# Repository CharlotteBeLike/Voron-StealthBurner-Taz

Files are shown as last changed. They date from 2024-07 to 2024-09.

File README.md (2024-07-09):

This was a fun challenge to put a Stealthburner onto my Taz 6.<br><br>
This mod may possibly be adaptable to the Taz Workhorse, Taz Pro, Taz Pro S, Taz Pro XT, Taz 5, Taz 4, Taz 3, Mini v1.04, Mini v1.03, and Kittaz :)<br>
Please be aware that none of this is perfect and you might have a few bumps along the way while building this. THERE ARE NO DOCS, so you will have to use the CAD model to assemble<br><br>

Printables: https://www.printables.com/model/543772-taz-56-to-stealthburner-v2<br><br>


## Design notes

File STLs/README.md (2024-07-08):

# Filename Nomenclature

| Category | Item | Amount |
|---|---|--|
| \*.stl | Base color |
| [a]\_\*.stl | Accent color |
| [c]\_\*.stl | Clear/Translucent (light can penetrate) |

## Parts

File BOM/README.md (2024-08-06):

# BOM

| Category | Item | Amount |
|---|---|---|
| Hardware | M3 X D5.0 X L4.0 Heat Set Insert| 22 |
| Hardware	| M3 Spring-Loaded T-Nut | 8 |
| Hardware	| M5 Spring-Loaded T-Nut	| 4 |
| Hardware	| Hotend Mounting Screws (M2.5/M3)	| 2-4 |
| Hardware	| M2x8 SHCS	| 2 |
| Hardware	| M2x10 SHCS	| 2 |
| Hardware	| M3x6 FHCS	| 3 |
| Hardware	| M3x6 BHCS	| 1 |
| Hardware	| M3x8 SHCS	| 14 |
| Hardware	| M3x10 SHCS	| 2 |
| Hardware	| M3x12 SHCS	| 12 |
| Hardware	| M3x16 SHCS	| 2 |
| Hardware	| M3x20 SHCS	| 1 |
| Hardware	| M3x25 SHCS	| 6 |
| Hardware	| M3x30 SHCS	| 1 |
| Hardware	| M3x40 SHCS	| 1 |
| Hardware	| M3x50 SHCS	| 2 |
| Hardware	| M3 Washer	| 1 |
| Hardware	| M3 Nut	| 2 |
| Hardware	| M5x12 SHCS	| 6 |
| Hardware	| 350mm 2020 V-Slot Extrusion	| 1 |
| Electronics	| NEMA14 36mm Round Pancake Motor with 10 tooth gear 20mm	| 1 |
| Electronics	| NEMA17 Stepper Motor	| 2 |
| Electronics	| DC 24V 5015 Centrefugal Fan	| 1 |
| Electronics	| DC 24V 4010 Axial Fan	| 1 |
| Electronics	| NeoPixel RGBW Mini Button PCB	| 3 |
| Electronics	| ADXL345 Accelerometer	| 1 |
| Electronics	| Rapido HF	| 1 |
| Electronics	| BL Touch	| 1 |
| Misc.	| Black Filament	| 1 |
| Misc.	| Lime Filament	| 1 |
| Misc.	| Lime Filament	| 1 |
| Misc.	| 6x3mm Magnet	| 1 |
| Misc.	| 3mmx4mm PTFE Tube 5M Length	| 1 |
| Printed | Parts	Z Carriage Right	| 1 |
| Printed | Parts	Z Carriage Left	| 1 |
| Printed | Parts	Rail Endstop	| 1 |
| Printed | Parts	Rail Endstop Mount	| 1 |
| Printed | Parts	Toolhead Hotend Front	| 1 |
| Printed | Parts	Toolhead Hotend Back	| 1 |
| Printed | Parts	Tensioner Slider	| 1 |
| Printed | Parts	X Carriage Frame Right	| 1 |
| Printed | Parts	X Carriage Frame Left	| 1 |
| Printed | Parts	Main Body	| 1 |
| Printed | Parts	Motor Plate	| 1 |
| Printed | Parts	[a]_Guilder A	| 1 |
| Printed | Parts	[a]_Guilder B	| 1 |
| Printed | Parts	[a]_Latch	| 1 |
| Printed | Parts	[a]_Shuttle	| 1 |
| Printed | Parts	[a]_Cover	| 1 |
| Printed | Parts	[c]_LED Carrier	| 1 |
| Printed | Parts	[c]_LED Diffuser Mask	| 1 |
| Printed | Parts	[c]_LED Diffuser | 1 |
| Printed | Parts	Cable Cover	| 1 |
| Printed | Parts	PCB Spacer (Optional)	| 1 |
| Printed | Parts	CW2 Chain Anchor For CANBUS (Optional)	| 1 |
| Printed | Parts	Printed Part For CAN Cable (Optional)	| 1 |
| Printed | Parts	Inductive Mount (Optional)	| 1 |
| Printed | Parts	BL Touch Mount (Optional)	| 1 |
| Printed | Parts	ADXL345 Screw Spacer (Optional)	| 2 |
| Motion	| 350mm MGN12H Linear Rail	| 1 |
| Motion	| Timing Pulley 20 teeth 5mm Bore	| 2 |
| Motion	| GATES-2GT	| 2 |
| Motion	| BMG Extruder Insides	| 1 |
| Cables	| MicroFit3 Male Pin	| 3 |
| Cables	| MicroFit3 Female Pin	| 3 |
| Cables	| MicroFit3 Connector Receptical 3 Position	| 1 |
| Cables	| MicroFit3 Connector Plug 3 Position	| 1 |
| Cables	| 30AWG PTFE Cable (3ft total)	| 1 |
| Cables	| 24AWG PTFE Cable (30ft total)	| 1 |

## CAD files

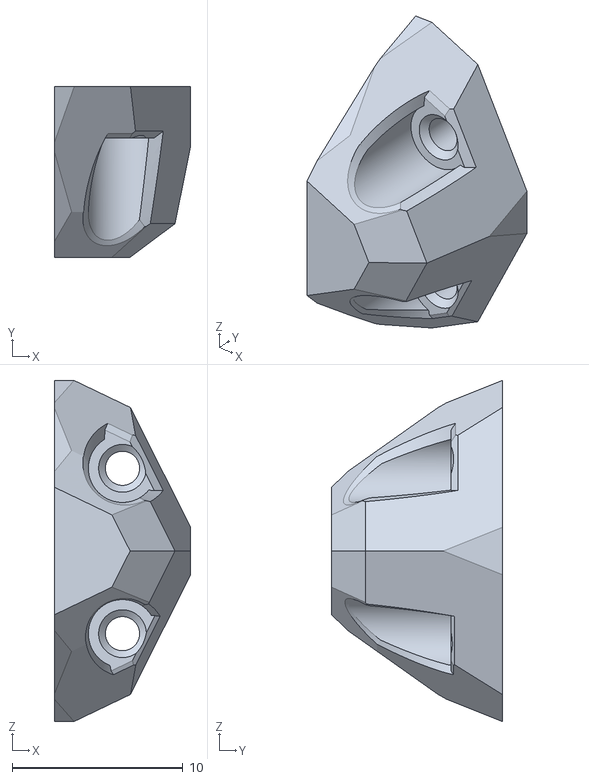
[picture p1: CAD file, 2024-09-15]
STLs/Rail Endstop.stl
8.00 x 10.0 x 20.0

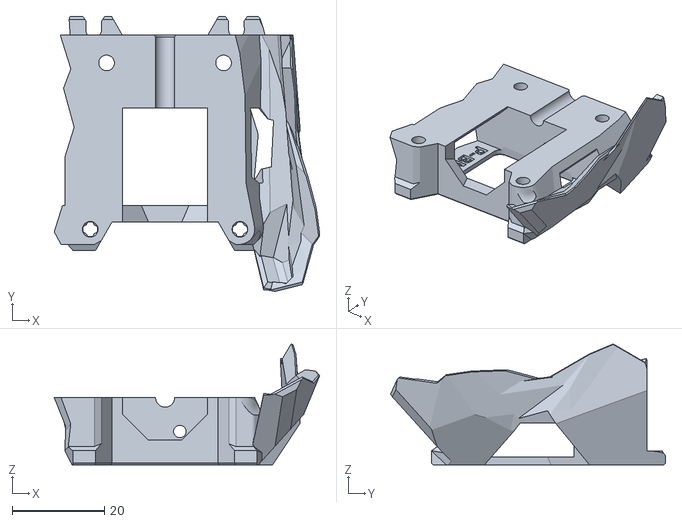
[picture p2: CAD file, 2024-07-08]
STLs/Stealthburner Printheads/phaetus_bmo/stealthburner_printhead_phaetus_bmo_rear_cw2.stl
57.7 x 59.7 x 26.3

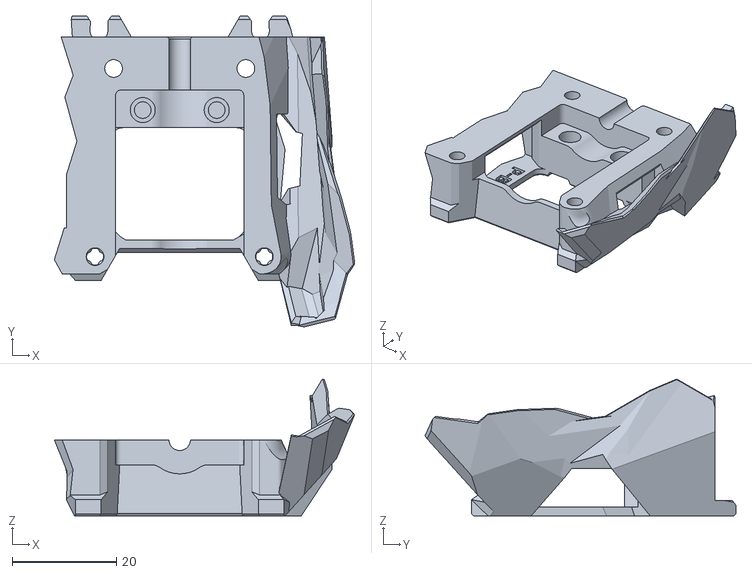
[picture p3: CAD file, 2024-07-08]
STLs/Stealthburner Printheads/phaetus_bms/stealthburner_printhead_phaetus_bms7_rear_cw2.stl
57.7 x 59.7 x 26.3

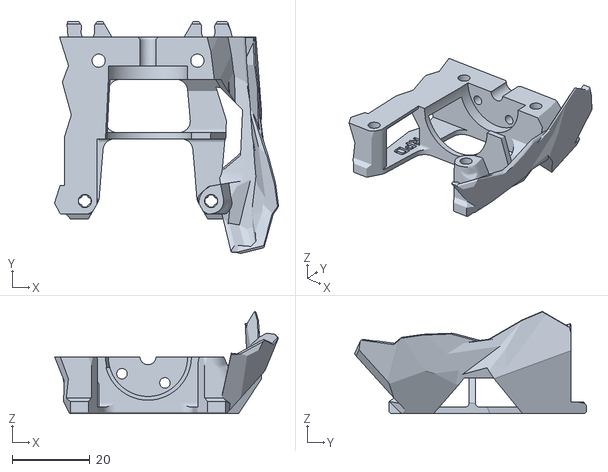
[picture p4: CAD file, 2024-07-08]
STLs/Stealthburner Printheads/phaetus_rapido/stealthburner_printhead_rapido_rear_cw2.stl
57.7 x 59.7 x 26.3

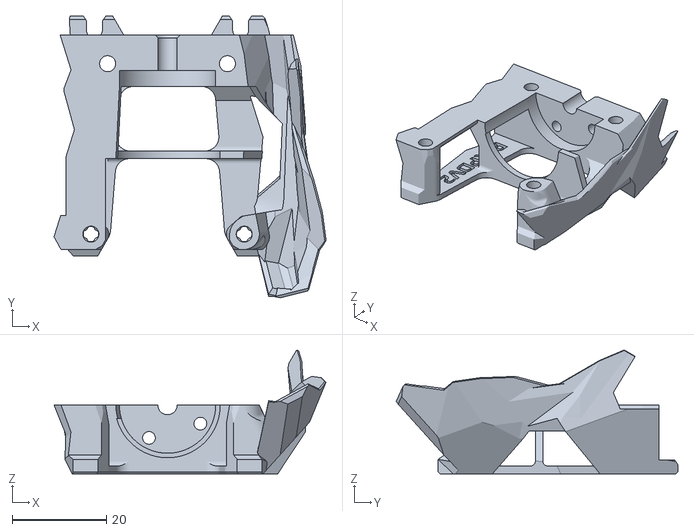
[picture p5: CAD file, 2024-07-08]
STLs/Stealthburner Printheads/phaetus_rapido_v2/stealthburner_printhead_rapido_v2_rear_cw1.stl
57.7 x 59.7 x 26.3

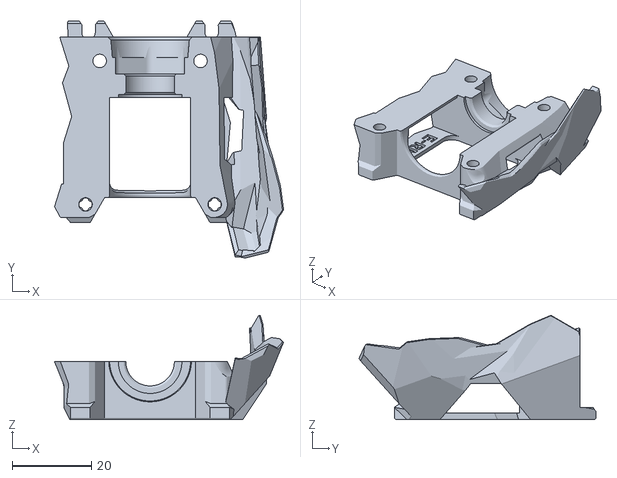
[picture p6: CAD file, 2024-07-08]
STLs/Stealthburner Printheads/revo_micro/stealthburner_printhead_revo_micro_rear_cw2.stl
57.7 x 59.7 x 26.3

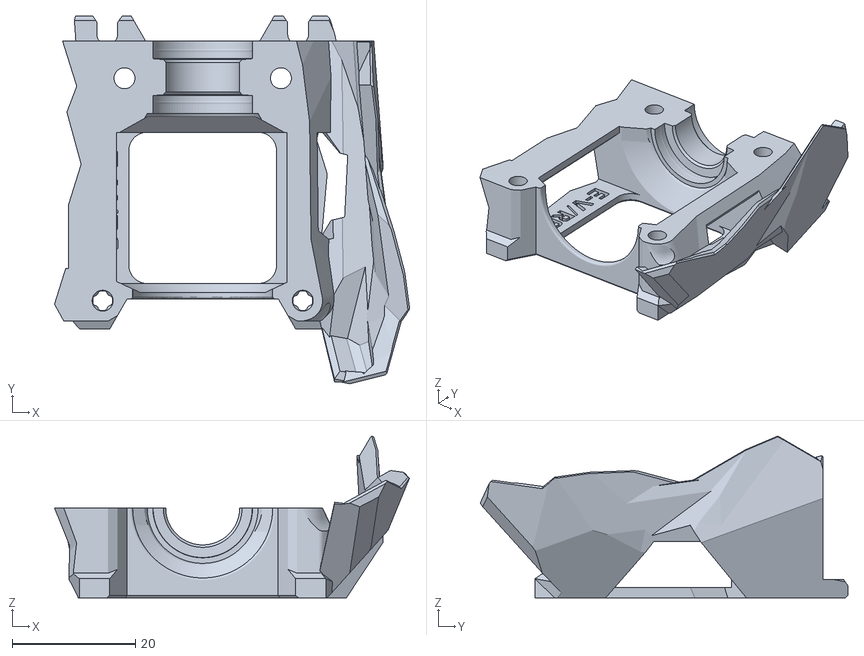
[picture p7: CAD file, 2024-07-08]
STLs/Stealthburner Printheads/revo_six_and_v6/stealthburner_printhead_v6_r6_rear_cw2.stl
57.7 x 59.7 x 26.3

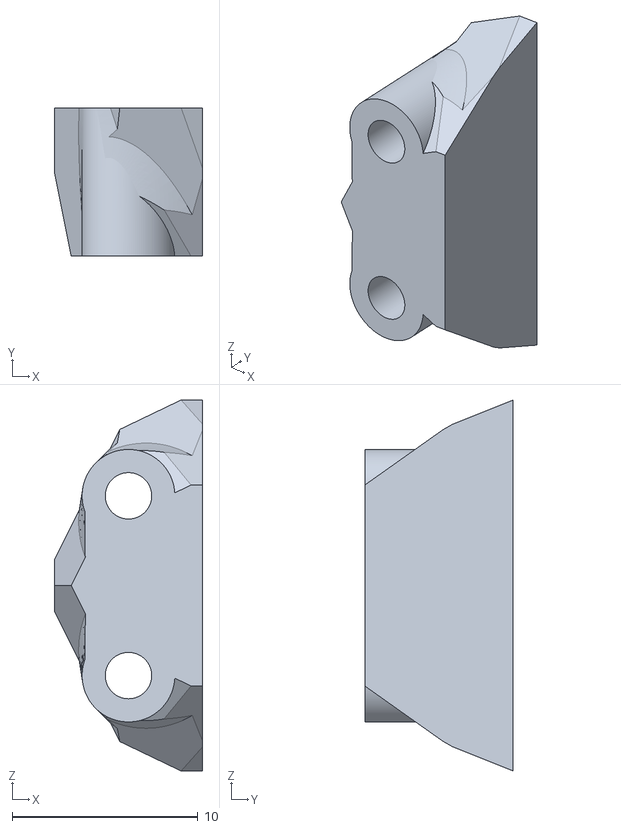
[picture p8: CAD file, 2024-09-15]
STLs/Rail Endstop Mount.stl
8.00 x 8.00 x 20.0

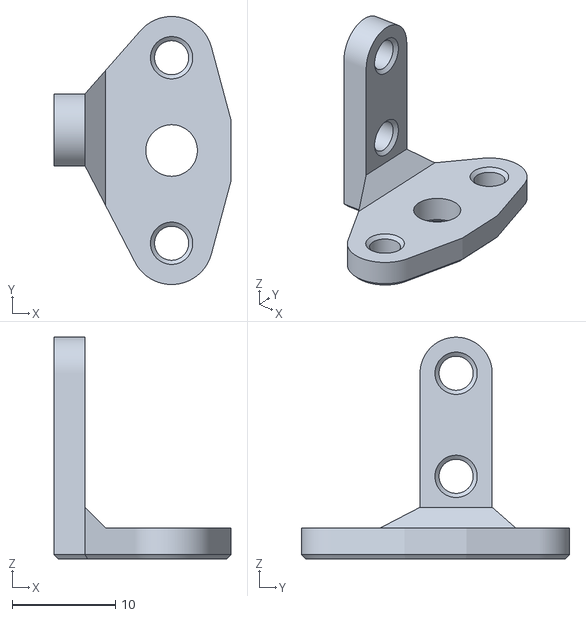
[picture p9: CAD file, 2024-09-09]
STLs/BL Touch Mount.stl
17.1 x 26.0 x 21.5

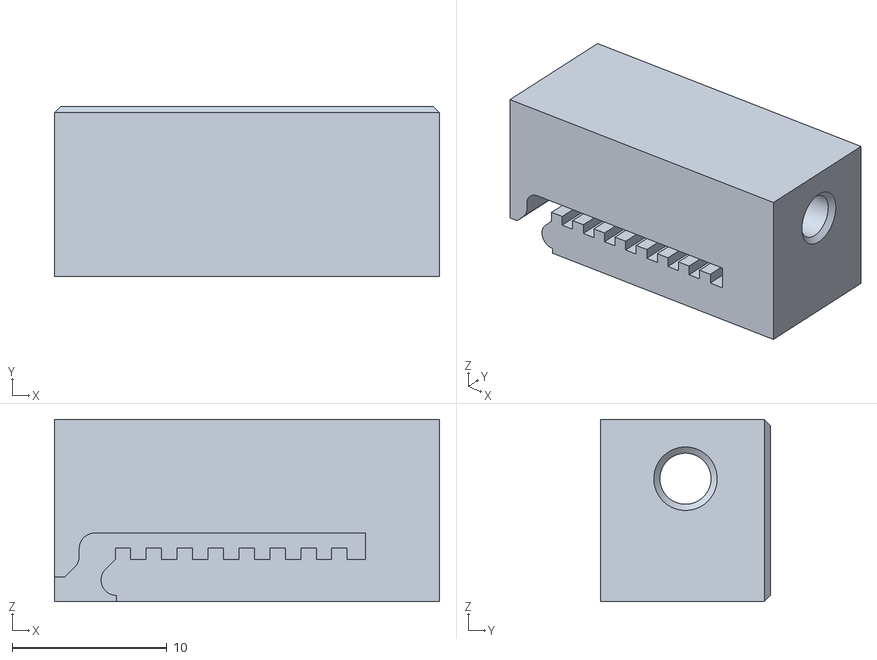
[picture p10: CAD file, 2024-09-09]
STLs/Tension Slider.stl
24.9 x 11.0 x 11.8

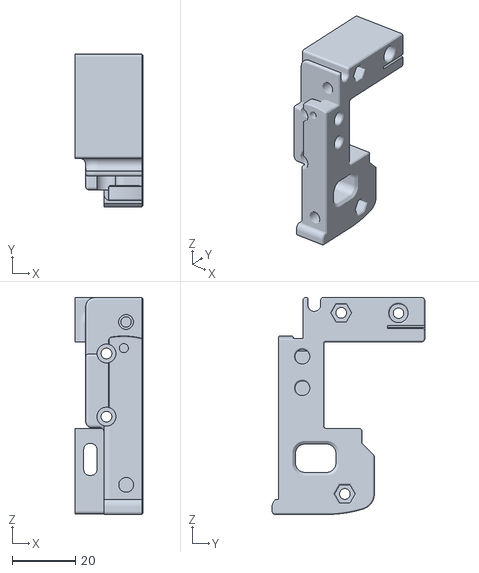
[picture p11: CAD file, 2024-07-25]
STLs/X Carriage Frame Right.stl
21.6 x 48.4 x 68.8

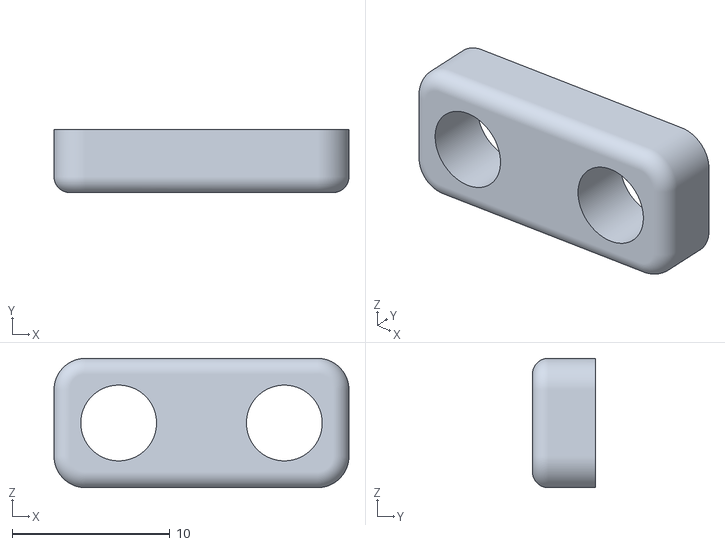
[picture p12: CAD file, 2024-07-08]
STLs/Inductive Mount.stl
18.7 x 4.00 x 8.20

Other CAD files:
STLs/Stealthburner Printheads/phaetus_dragon/stealthburner_printhead_dragon_rear_cw2.stl
STLs/Stealthburner Printheads/revo_voron/stealthburner_printhead_revo_voron_rear_cw2.stl
STLs/Stealthburner Printheads/phaetus_bmo/stealthburner_printhead_phaetus_bmo_rear_cw1.stl
STLs/Stealthburner Printheads/phaetus_bms/stealthburner_printhead_phaetus_bms6_rear_cw2.stl
STLs/Stealthburner Printheads/phaetus_rapido_v2/stealthburner_printhead_rapido_v2_rear_cw2.stl
STLs/X Carriage Frame Left.stl
STLs/ADXL345 Mount.stl
STLs/ADXL345 Screw Spacer.stl
STLs/CW2 Chain Anchor For CANBUS.stl
STLs/Cable Cover For PCB.stl
STLs/Printed Part For CAN Cable.stl
STLs/[c]_LED Carrier.stl
STLs/[c]_LED Diffuser Mask.stl
STLs/[c]_LED Diffuser.stl

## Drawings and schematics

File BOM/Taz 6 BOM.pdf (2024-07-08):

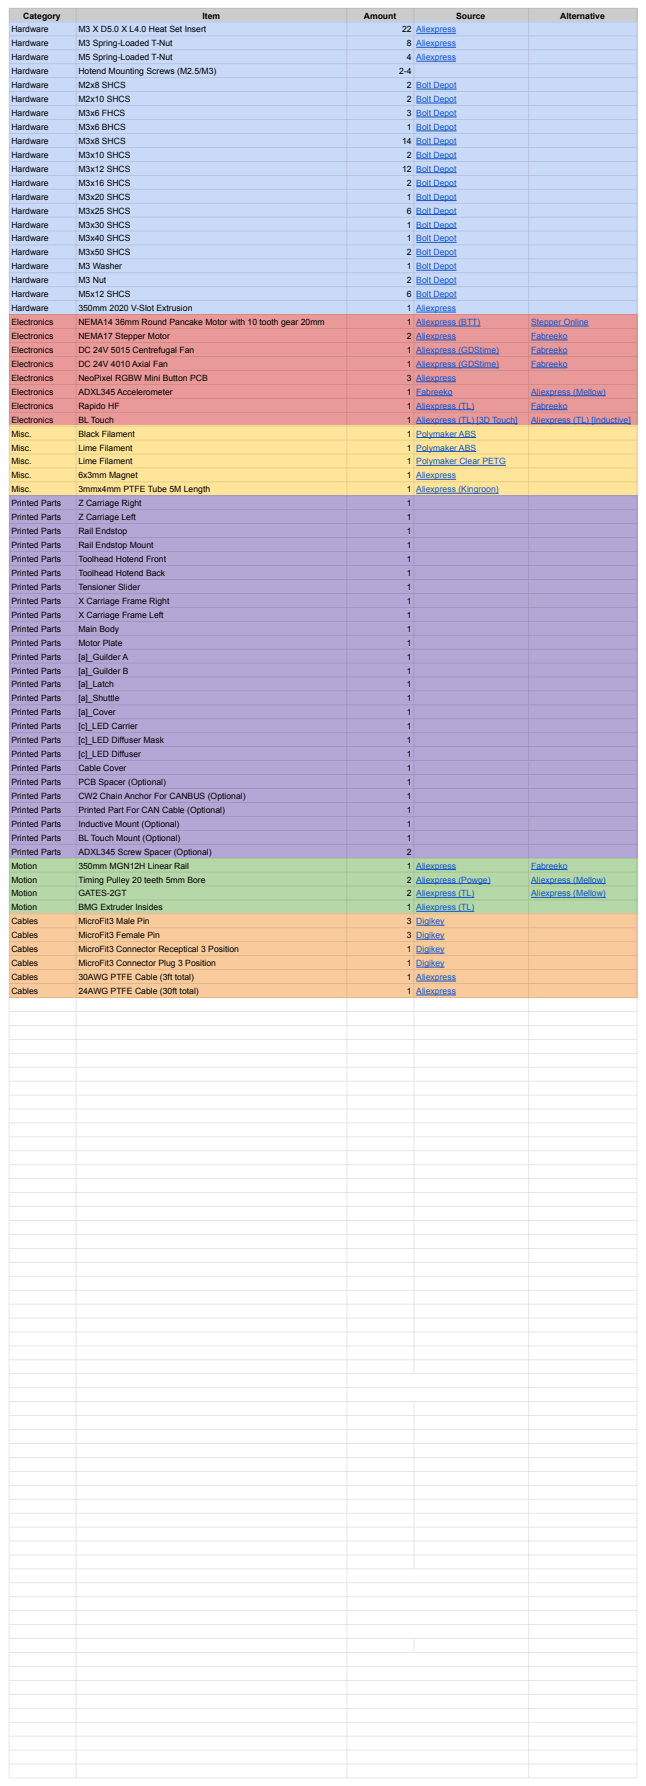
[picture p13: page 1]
Category; Item; Amount; Source; Alternative Hardware; M3 X D5.0 X L4.0 Heat Set Insert; 22 Aliexpress Hardware; M3 Spring-Loaded T-Nut; 8 Aliexpress Hardware; M5 Spring-Loaded T-Nut; 4 Aliexpress Hardware; Hotend Mounting Screws (M2.5/M3); 2-4 Hardware; M2x8 SHCS; 2 Bolt Depot Hardware; M2x10 SHCS; M3x6 FHCS; 3 Bolt Depot Hardware; M3x6 BHCS; 1 Bolt Depot Hardware; M3x8 SHCS; 14 Bolt Depot Hardware; M3x10 SHCS; M3x12 SHCS; 12 Bolt Depot Hardware; M3x16 SHCS; M3x20 SHCS; M3x25 SHCS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

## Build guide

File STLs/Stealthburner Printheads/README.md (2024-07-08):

# Printheads for Stealthburner.

Choose files containing ***front*** based on your hotend and ***rear_cw1*** / ***rear_cw2*** based on whether you're using the original Clockwork (CW1) or the new Clockwork2 (CW2) extruder.

## Printhead Compatibility:

| Hotend | Compatible Parts | Mounting Hardware | Notes |
| :---: | :---: | :---: | :---:
| Phaetus/Trianglelab Dragon ST/SF/HF | (P-DRG) | 4x M2.5x8mm | Remove the screws attaching the groove-mount adaptor to access the hard mounting points. |
| Phaetus BMO | (P-BMO) | 4x M2.5x8mm | Unscrew the groove-mount adaptor to access the hard mounting points. |
| Phaetus BMS (6 fins) | (P-BMS6) | 2x M3x12mm | Phaetus has two versions of the BMS; Count the number of fins on your hotend to determine your version. |
| Phaetus BMS (7 fins) | (P-BMS7) | 2x M3x12mm | Phaetus has two versions of the BMS; Count the number of fins on your hotend to determine your version. |
| Phaetus Rapido | (P-RPD) | 4x M2.5x8mm | Only the standard Rapido is supported (No UHF support). See the additional note about [heatsink orientations](phaetus_rapido/README.md). |
| E3D Revo Micro | (E-RM) | M12x1.5mm Plastic Nut | If your mount nut has a ridge on it, put that to the top. |
| E3D Revo Six | (E-V/R6) | N/A |  |
| E3D V6 | (E-V/R6) | N/A |  |
| E3D Revo Voron | (E-RV) | 4x M3x8mm |  |

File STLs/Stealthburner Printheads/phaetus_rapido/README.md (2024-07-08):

## Phaetus Rapido High Flow mount

### BOM

- One front printed part
- One rear printed part
- Heatset inserts
- Four M2.5x8 socket screws, which should be provided in your Rapido kit
- Two M3x12 socket screws
- PTFE tube

### Instructions

- Add two heatset inserts on the front printed part. Add an additional two if you plan to use the ADXL PCB mount.
- Remove the adapter and bowden collet from the Rapido's heatsink by unscrewing the two M2.5x5 screws:
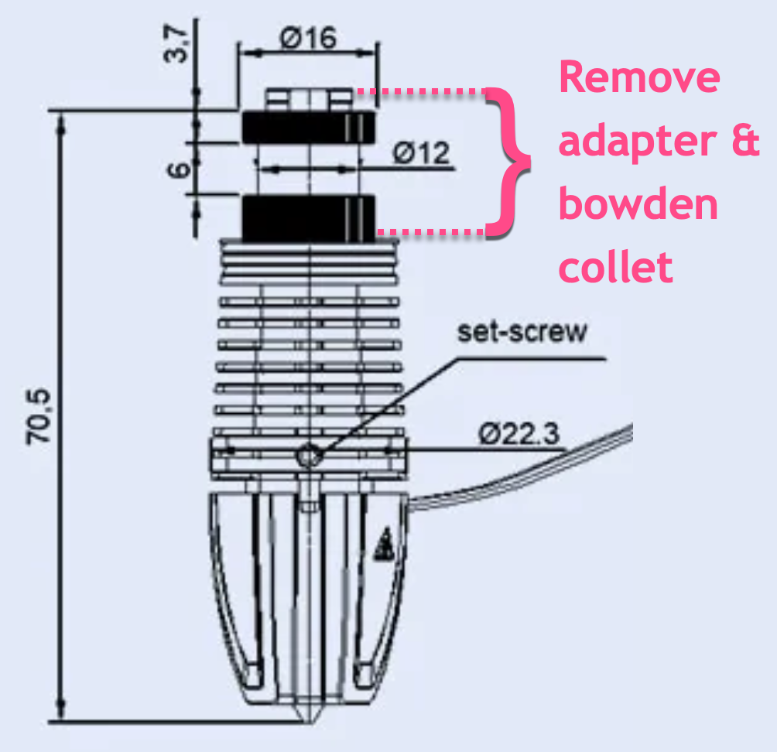
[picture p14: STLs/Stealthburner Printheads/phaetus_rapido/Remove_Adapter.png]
Remove adapter
  
- Place the hotend in the front printed part and secure it by screwing two M2.5x8 screws into the heatsink.
- Secure the front and rear printed parts together with two M3x12 screws.
- Secure the hotend with the rear part by screwing two M2.5x8 screws into the heatsink.
- Insert the PFTE tube at the top of the mount.

### A note about Rapido orientations

Depending on where the Rapido is sourced, it may come in one of two _unsupported_ heatsink orientations.

To change the orientation of heatsink to a supported orientation:

1. Loosen the grub screw on the side.
2. Remove the 3 screws around the heater core.
3. Rotate the heatsink +/- 120° into the correct orientation (see the pictures below).
4. Install and _gently tighten_ the 3 screws around the heater core.
5. _Gently tighten_ the side grub screw.
6. **Be careful not to over-tighten any screws when reassembling.**  Over-tightening can cause the heatbreak to bend and potentially restrict the filament path. Checking for smooth filament movement through a cold hotend without a nozzle is recommended prior to reinstalling the Rapido into the printhead.

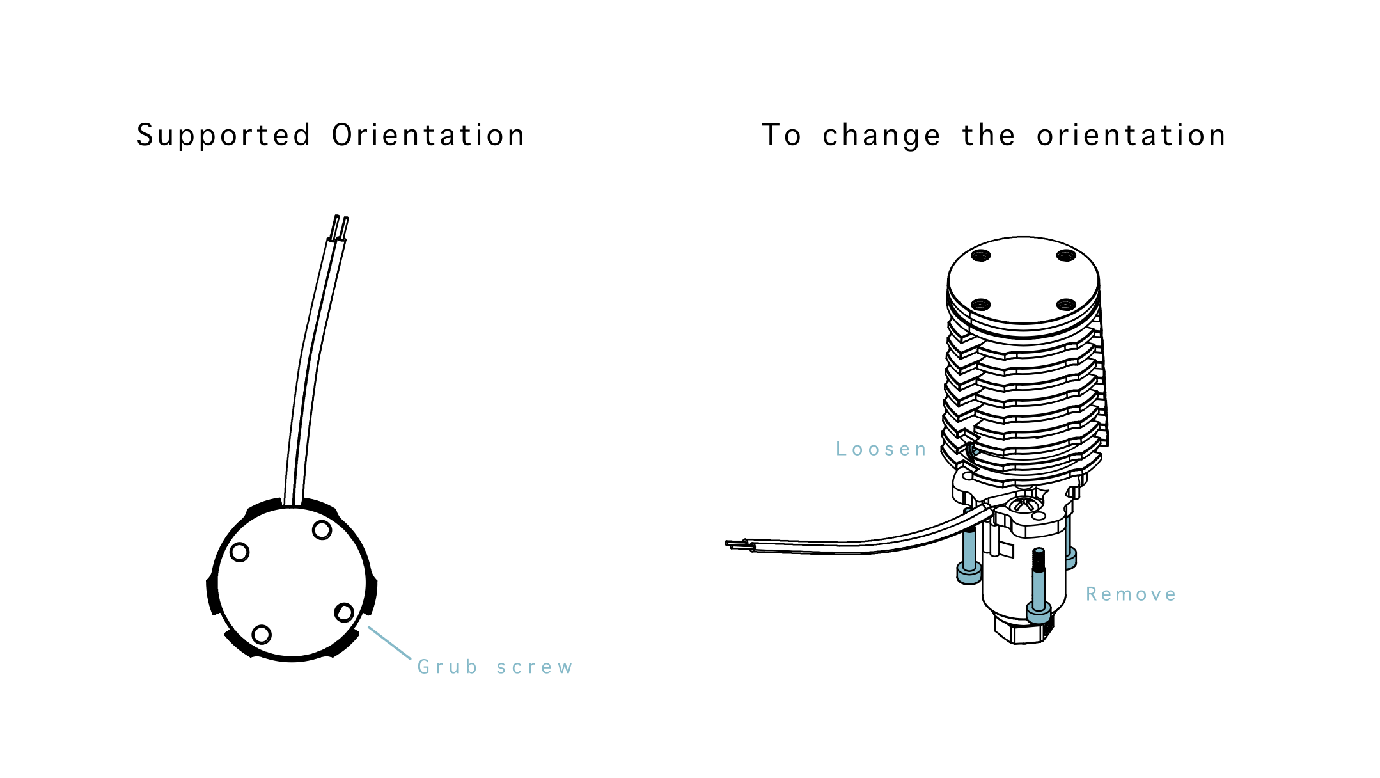
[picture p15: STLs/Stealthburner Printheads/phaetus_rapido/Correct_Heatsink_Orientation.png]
Correct Heatsink Orientation


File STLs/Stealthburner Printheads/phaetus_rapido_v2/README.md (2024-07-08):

## Phaetus Rapido High Flow mount

### BOM

- One front printed part
- One rear printed part
- Heatset inserts
- Four M2.5x8 socket screws, which should be provided in your Rapido kit
- Two M3x12 socket screws
- PTFE tube

### Instructions

- Add two heatset inserts on the front printed part. Add an additional two if you plan to use the ADXL PCB mount.
- Remove the adapter and bowden collet from the Rapido's heatsink by unscrewing the two M2.5x5 screws:
  Remove adapter
- Place the hotend in the front printed part and secure it by screwing two M2.5x8 screws into the heatsink.
- Secure the front and rear printed parts together with two M3x12 screws.
- Secure the hotend with the rear part by screwing two M2.5x8 screws into the heatsink.
- Insert the PFTE tube at the top of the mount.

### A note about Rapido orientations

Depending on where the Rapido is sourced, it may come in one of two _unsupported_ heatsink orientations.

To change the orientation of heatsink to a supported orientation:

1. Loosen the grub screw on the side.
2. Remove the 3 screws around the heater core.
3. Rotate the heatsink +/- 120° into the correct orientation (see the pictures below).
4. Install and _gently tighten_ the 3 screws around the heater core.
5. _Gently tighten_ the side grub screw.
6. **Be careful not to over-tighten any screws when reassembling.**  Over-tightening can cause the heatbreak to bend and potentially restrict the filament path. Checking for smooth filament movement through a cold hotend without a nozzle is recommended prior to reinstalling the Rapido into the printhead.

**The following is an example for the Rapido V1 hotend, but the process is the same for the V2. Take care to ensure you are using the correct orientation for the V2, the following image just explains the process.**

Correct Heatsink Orientation for Rapido V1

Use the above process to adjust the heatsink orientation for the V2. Be sure that the heatbrake set screw, thermistor wires, and heater wires are all aligned as shown below:

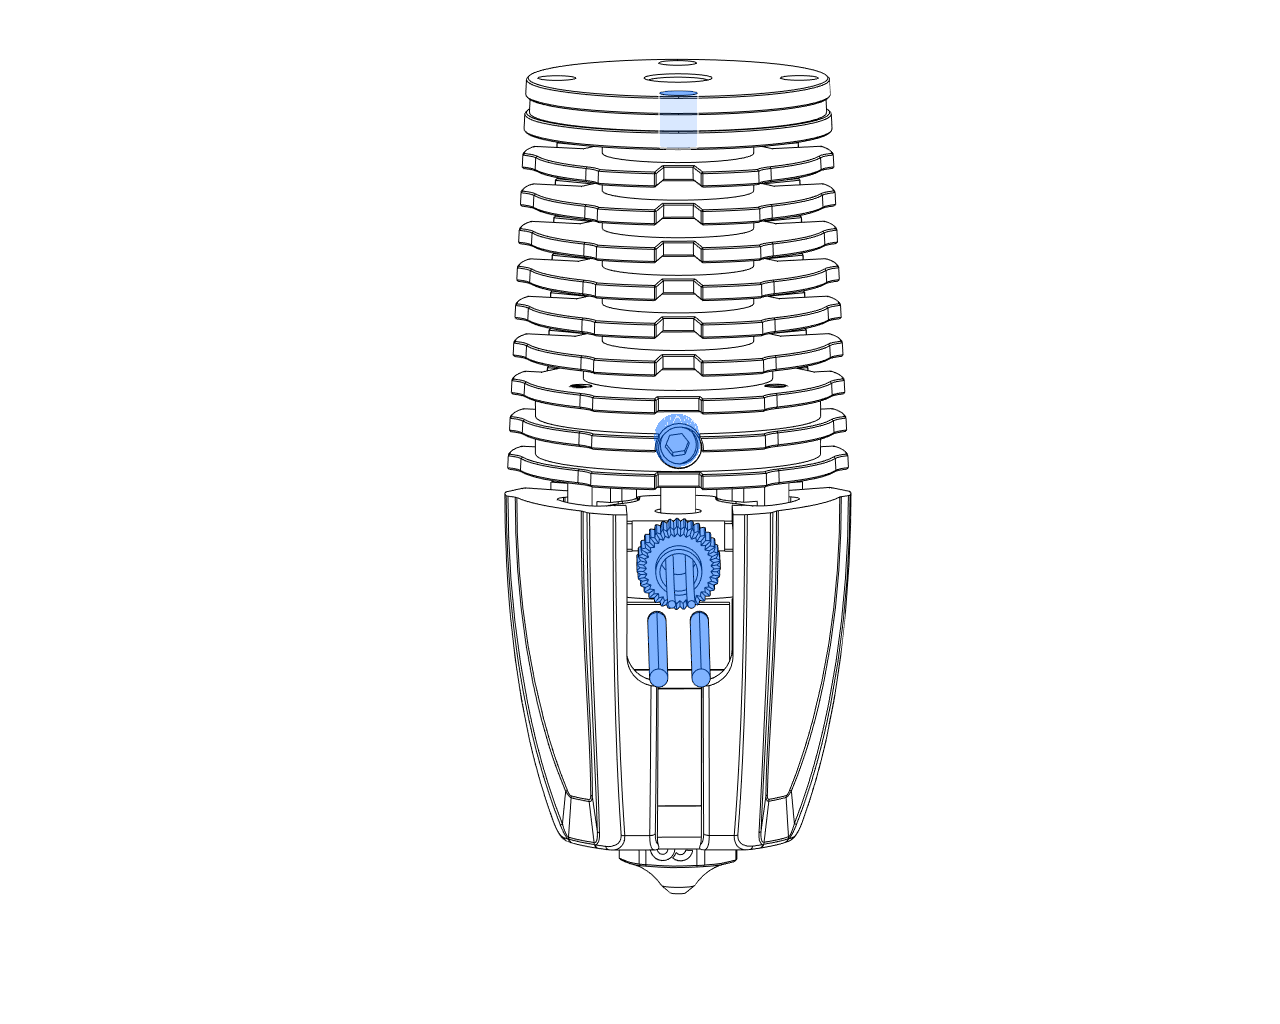
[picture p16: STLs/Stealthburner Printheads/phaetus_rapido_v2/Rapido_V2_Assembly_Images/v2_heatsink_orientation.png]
Correct Heatsink Orientation


After you've aligned the heatsink as shown above, you will need to slightly bend the heater wire strain relief tab (if any) downward.
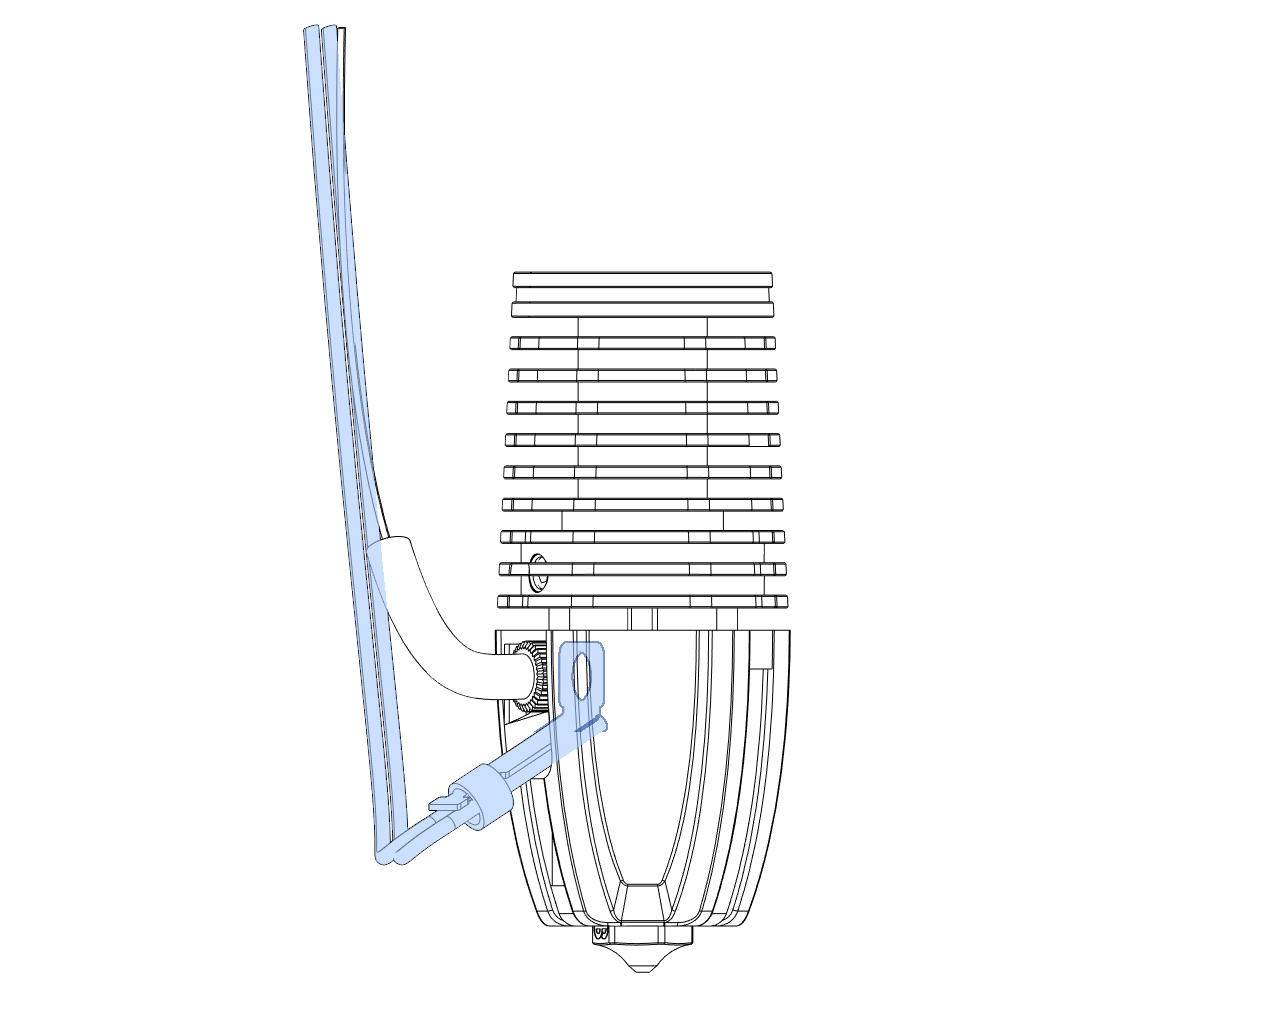
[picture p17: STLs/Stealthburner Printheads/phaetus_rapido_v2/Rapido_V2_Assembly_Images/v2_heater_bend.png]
Bend the strain relief down


After bending the heater wires downward, fit the Rapido V2 into the front half of the SB ducts, and check to make sure you've got the heater wires routed below the mounting screw boss, and the thermistor wires routed above the mounting screw boss as shown here:
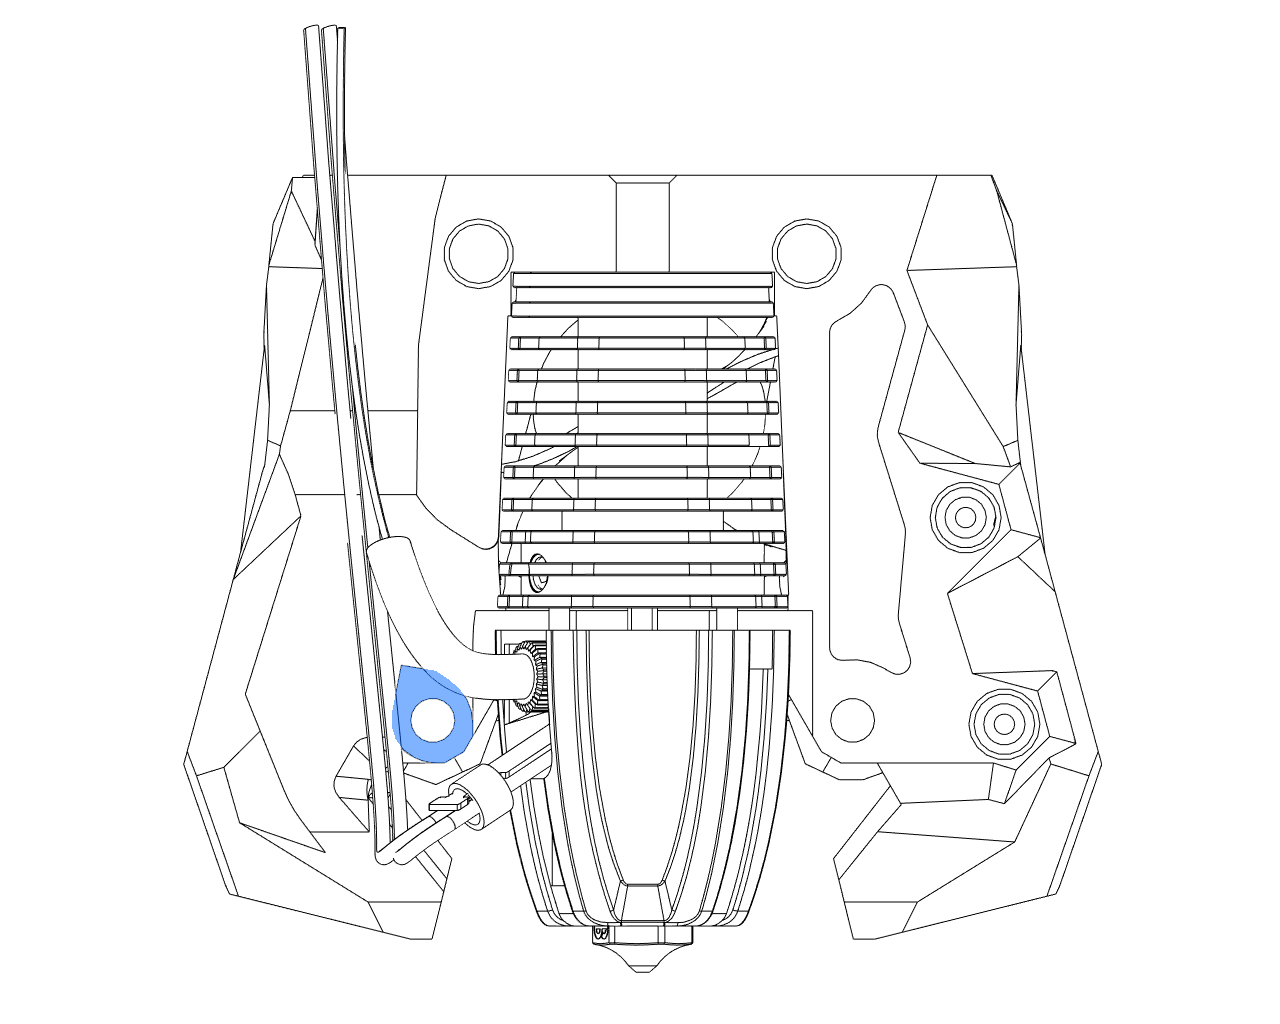
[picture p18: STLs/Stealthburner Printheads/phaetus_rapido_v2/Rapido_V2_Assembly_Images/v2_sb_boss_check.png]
Check wire location relative to mounnting screw boss


Now install the back half of the SB ducts, and you are done!

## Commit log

2024-03-30 Rename Print Plate - Main Body.stl to Main Body.stl
    [Main Body.stl, Print Plate - Main Body.stl]
2024-03-30 Rename Print Plate - Motor Plate.stl to Motor Plate.stl
    [Motor Plate.stl]
2024-03-30 Rename Print Plate - [support]_Cable Cover For PCB.stl to [support]_Cable Cover For PCB.stl
    [[support]_Cable Cover For PCB.stl]
2024-03-31 Rename Print Plate - X-Axis Belt Mount.stl to X-Axis Belt Mount.stl
    [X-Axis Belt Mount.stl]
2024-03-31 Rename Print Plate - [support]_SB Carriage.stl to [support]_SB Carriage.stl
    [Print Plate - [support]_SB Carriage.stl, [support]_SB Carriage.stl]
2024-03-31 Rename Print Plate - Carriage Spacer.stl to Carriage Spacer.stl
    [Carriage Spacer.stl]
2024-03-31 Rename [a]_Cover Triangle.stl to [a]_Stealthburner Main Body Triangle.stl
    [[a]_Stealthburner Main Body Triangle.stl]
2024-03-31 Rename [a]_Cover Octopus.stl to [a]_Stealthburner Main Body Octopus.stl
    [[a]_Stealthburner Main Body Octopus.stl]
